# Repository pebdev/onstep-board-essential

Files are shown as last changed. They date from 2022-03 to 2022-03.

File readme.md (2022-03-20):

## Description

[OnStep](https://onstep.groups.io/g/main/wiki) is an open source project to control a telescope mount (goto). 

Essential board is an hardware solution which use OnStep with the essential parts only :

- ESP32 to run OnStep
- 3 axis controller (DE, RA and focuser)
- GPS (time and location)
- Humidity, barometric pressure and ambient temperature sensors

**This project provides :**

- Design of the Essential board
- Updated OnStep project for this board

**Main components :**

- (x1) **Essential board** (this project)

- (x1) **ESP32-WROOM DEVKIT**

- (x1) **ATGM336H** gps

- (x1) **BME208** sensor

- (x3) **Nema17** motor 0.9° (DE, RA and focuser)

  ```
  Manufacturer Part Number: 17HS4401 (42BYGH)
  Motor Type: Bipolar Stepper
  Step Angle: 0.9 deg.
  Step : 400
  Holding Torque: 280 mM.m
  Rated Current/phase: 1.3A
  Shaft Diameter: 5mm
  Number of Leads: 4
  Weight: 280g
  ```
  
- (x3) **TMC2225** stepper motor driver

  ```
  Manufacturer Part Number: TMC2225
  Motor voltage: 4.75V-36V DC
  Max output current (RMS): 1.4A
  Max output current (peak): 2.0A
  ```

## Hardware change

ESP32 board has a big defect, it resets when a serial connection is opened, caused by RTS (Ready To Send) if it's enabled.

it's a problem because GPS isn't ready when PC/MAC application request position at startup.

For this reason, a patch must be applied :

- R22 resistance must be turned by 90°
- un push button must be welded  between the resistance and the empty pad

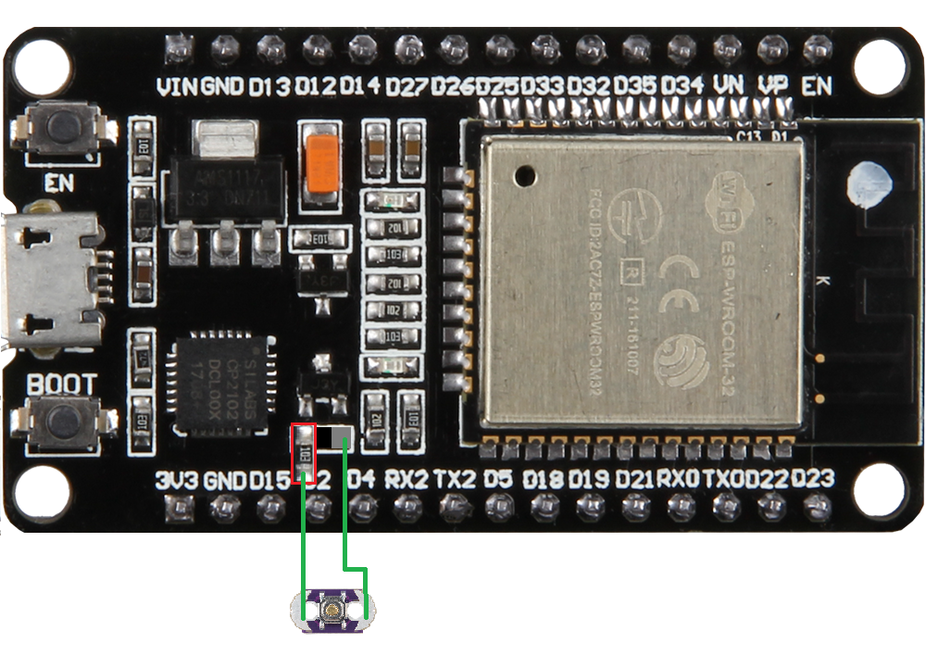
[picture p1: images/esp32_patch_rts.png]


## Fetch project

Be sure that you have the Essential branch of OnStep :

  ```
  git submodule update --init --recursive
  git checkout board-essential-v1
  ```

## Installation

### Xcode
Because we use tools provided with Xcode, install it from the AppleStore.
When it's done start it and install proposed tool.

**Note :** when a new major version of the SDK (12.x to 13.x) is installed, an issue can occure.

It can be fixed by using these commands :

```
sudo xcode-select --reset
sudo xcode-select -s /Applications/Xcode.app/Contents/Developer
```

### ESP32 board support

This project use ARDUINO environment, install it before to start and follow these steps :

**1-** Open **OnStep.ino** file from Arduino application

**2-** Add ESP32 board support to Arduino :

- Select *Arduino > Preferences* "Additional Boards Manager URLs"
  - add: **https://dl.espressif.com/dl/package_esp32_index.json**
- Install support for this board from within the menu *Tools > Board > Boards Manager*
  - Seach for esp32 and install the version **1.0.4 only**

**3-** Select ESP32 board for the project :

- Tools > Board Type > ESP32 Arduino > ESP32 Dev Module

### Libraries

#### TinyGPSPlus

**1-** Download sources from github : [link](https://github.com/mikalhart/TinyGPSPlus/archive/refs/heads/master.zip)

**2-** Install it with Arduino GUI :

- Sketch > Include Library > Add .zip Library ...
- Select the zip file (or folder because OSX unzip it after downloading)
- Now you can delete zip file or folder

#### Adafruit BMP280 Library

**1-** Install it with Arduino GUI :

- Tools > Manage Libraries
- Install Adafruit BMP280 Library

## Build

Nothing special, just build the code.

If you have this error when you build OnStep :

```
ValueError: dlsym(RTLD_DEFAULT, kIOMasterPortDefault): symbol not found
```

Follow these steps :

1- Install **python3 (3.10)** with MacPorts (or Homebrew, etc)
```
sudo port install python310
```

2- Install **pip** tool
```
sudo port install py310-pip
```

3- Install **pyserial** package :

```
python -m pip install pyserial
```

3- Update esptool :

```
cd ~/Library/Arduino15/packages/esp32/tools/esptool_py/2.6.1
mv esptool esptool.orig
curl https://raw.githubusercontent.com/espressif/esptool/master/esptool.py -o esptool
chmod +x esptool
```

If you still get the same `symbol not found` error then open **esptool** and change the first line from `#!/usr/bin/env python` to `#!/usr/local/bin/python3`.

or 

`sed -i -e 's/=python /=python3 /g' ~/Library/Arduino15/packages/esp32/hardware/esp32/*/platform.txt`

## How to flash the board

According the ESP32 hardware patch that we applied, it's mandatory to follow these steps to reflash the board :

- Start flahing with ARduino IDE
- When Arduino IDE try to send application to the ESP32, push the push button that we welded before
- When flashing is started, release this button

## Validation

This project was tested with these parts :

- Bresser EQ3 mount, with custom goto addon : [stl files](https://cults3d.com/fr/modèle-3d/divers/bresser-eq3-motor-addon)
- Telescope application (OSX)

A simple way to test if OnStep is alive on the board, use a serial terminal and enter this command :

```
:GVP#
```

All commands of OnStep can be found [here](https://onstep.groups.io/g/main/wiki/23755).

## Customization ##

According your mount, you must change values of your gear ratios.

**1-** Use this [excel sheet](https://baheyeldin.com/sites/baheyeldin.com/files/OnStep-Calculations.xls) to calculate data for your mount

**2-** Update these defines into the **config.h** file in the Arduino project

## Contribute

To use latest version of the upstream repository :

```shell
git remote add upstream https://github.com/hjd1964/OnStep
```

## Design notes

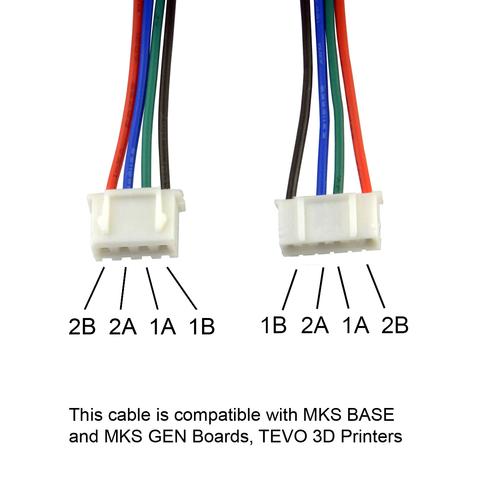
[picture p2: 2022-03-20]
altium/stepper_motor_connectors.jpg

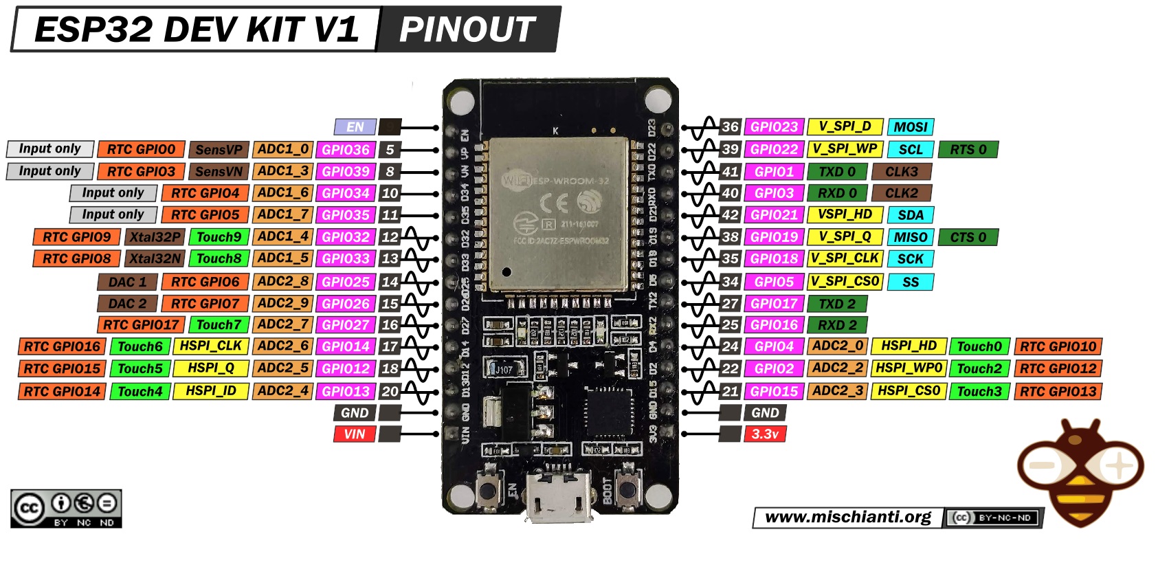
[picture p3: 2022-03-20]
altium/esp32.jpg

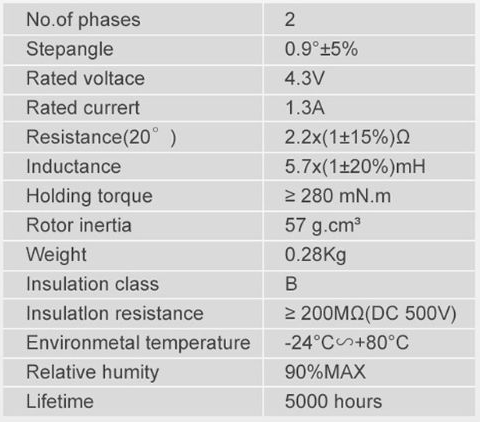
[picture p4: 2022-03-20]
altium/motor_17HS4401.PNG

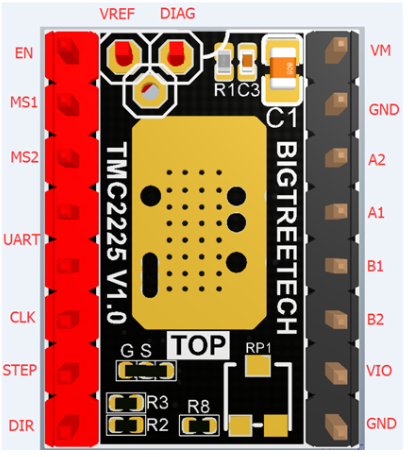
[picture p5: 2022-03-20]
altium/tmc2225.PNG

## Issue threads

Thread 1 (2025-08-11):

More info

Sylvain-BROCAS, 2025-08-11:
Hello,
Thank you for your work. I would love to use it as a base for a project. Do you mind to share some pictures of the final pcb and some generic files for the pcb (I don't have altium, but kicad so a gerber would be great).

Thank you
Sylvain

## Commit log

2022-02-13 Altium project (v2)
    [onStep-board-power.SchDoc, onStep-board-uc.SchDoc, onStep-board.PrjPcb]
2022-03-19 Dependency update : use first version of OnStep with Essential board
2022-03-20 Updated documentation of the Altium project
    [onStep-board-power.SchDoc, onStep-board-uc.SchDoc]
2024-01-27 latest version before stopping the project
    [onStep-board-power.SchDoc, onStep-board-uc.SchDoc, onStep-board.PrjPcb]
